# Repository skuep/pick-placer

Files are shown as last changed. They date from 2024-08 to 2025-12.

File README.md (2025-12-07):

Pick-Placer
===========
This is work in progress and highly beta.

Onshape CAD Data is here: https://cad.onshape.com/documents/7a2b90e013ddb4f790097381/w/de934a112d86b578c597cdf9/e/dd9aa8bcdc6310fd48dbadf3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

This is a mix of multiple projects:
---------

- LumenPnP
  - Basic Idea and Toolhead Design
  - Valves, 260mm Belt, Nema 11 Rotation Motors (later switched to Juki style from Robotdigg)
  - Cameras (ELP 720P USB kamera modul CMOS OV9712 mit 6mm Fokus) & ring-lights (slightly modified)
  - Staging plate (modified to measure 90x470)
  - Photon feeder support (mechanical, not tested)
  - Datum board & mount (modified)
  - Toolhead Linear Rails
  
- Voron Trident 350mm
  - Frame Kit (plus a few uncritical saw cuts and blind joint holes using jigs) and Panels
  - X/Y Motors, Belts, MGN12 and MGN9 Rails for X/Y
  - Nema14 stepper motor (~~17HS08-1004S~~ 17HS19-2004S1)
  - Split toolhead carriage design and XY joint design
  - X/Y Drag Chains
  - Idlers (BFI)
  - D2F homing switch PCB
  - Rubber feet
  - DIN Rails
  - Screws & Misc Hardware
  - Belt routing idea (plus some inspiration from VzBoT-330)

Other Parts used:
- Festo CRVZS-0,4 (Used on ebay)
- MGN9C 100mm Rails (CNA on AliExpress)
- Nema17 stepper motor with 20mm thickness (Stepper-Online) for Toolhead
- 500mm length extrusions with V groove for LumenPnP feeder compatibility
- 32 Teeth pulleys

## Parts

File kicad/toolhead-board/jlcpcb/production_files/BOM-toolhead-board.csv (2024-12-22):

Comment | Designator | Footprint | LCSC
100R | FB1 | R_0805_2012Metric | C1015
22u/10V/X5R | C10 | C_1206_3216Metric | C12891
10u/50V/X5R | C9 | C_1206_3216Metric | C13585
100n | C1,C11,C2,C8 | C_0603_1608Metric | C14663
UA9637 | U6 | SO-8_3.9x4.9mm_P1.27mm | C1544610
1n | C4,C5 | C_0603_1608Metric | C1588
4.7u/16V | C3 | C_0603_1608Metric | C19666
TLV6001DCK | U7,U8 | SOT-353_SC-70-5 | C2059411
MIC5233-5.0YM5-TR | U3 | SOT-23-5 | C219988
10R | R1,R11,R12,R15,R16,R2,R3,R6,R7,R8 | R_0603_1608Metric | C22859
5.1K | R10,R4,R5,R9 | R_0603_1608Metric | C23186
24K | R14 | R_0603_1608Metric | C23352
100K | R13 | R_0603_1608Metric | C25803
1uF/50V | C6 | C_0805_2012Metric | C28323
LMZM23601 | U5 | Texas_SIL0010A_MicroSiP-10-1EP_3.8x3mm_P0.6mm_EP0.7x2.9mm_ThermalVias | C2861484
74LVC1G17GW | U4 | SOT-353_SC-70-5 | C426705
USB_C_Receptacle_USB2.0 | J9 | MC-711 | C6332301
MountingHole | H3 | MountingHole_3.2mm_M3
MountingHole | H2 | MountingHole_3.2mm_M3
CAM | J10 | JST_PH_B4B-PH-K_1x04_P2.00mm_Vertical
RGB | J5 | JST_XH_B3B-XH-A_1x03_P2.50mm_Vertical
XGZP6857A100KPGPN | U2 | XGZP6857A
ZES | J8 | JST_PH_B4B-PH-K_1x04_P2.00mm_Vertical
MountingHole | H5 | MountingHole_3.2mm_M3
VR | J7 | JST_XH_B2B-XH-A_1x02_P2.50mm_Vertical
Conn_01x08 | J12 | JST_XH_S8B-XH-A-1_1x08_P2.50mm_Horizontal
DB9_Male_MountingHoles | J11 | DSUB-9_Male_Horizontal_P2.77x2.84mm_EdgePinOffset4.94mm_Housed_MountingHolesOffset7.48mm
VL | J6 | JST_XH_B2B-XH-A_1x02_P2.50mm_Vertical
XGZP6857A100KPGPN | U1 | XGZP6857A
MountingHole | H6 | MountingHole_3.2mm_M3
Conn_02x12_Top_Bottom | J1 | Molex_Micro-Fit_3.0_43045-2400_2x12_P3.00mm_Horizontal
RM | J4 | JST_XH_B4B-XH-A_1x04_P2.50mm_Vertical
ZM | J2 | JST_XH_B4B-XH-A_1x04_P2.50mm_Vertical
LM | J3 | JST_XH_B4B-XH-A_1x04_P2.50mm_Vertical

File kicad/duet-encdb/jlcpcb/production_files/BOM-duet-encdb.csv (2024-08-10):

Comment | Designator | Footprint | LCSC
1u/10V | C2,C5,C7 | C_0603_1608Metric | C15849
10u/10V | C1,C3,C4,C6 | C_0805_2012Metric | C15850
100R | R1,R2,R3,R4,R5,R6 | R_0603_1608Metric | C22775
10K | R10,R11,R12,R7,R8,R9 | R_0603_1608Metric | C25804
LM2775DSG | U1,U2 | WSON-8-1EP_2x2mm_P0.5mm_EP0.9x1.6mm_ThermalVias | C473361
74LVC541A | U3 | TSSOP-20_4.4x6.5mm_P0.65mm | C6093
Conn_01x08 | J3 | JST_XH_B8B-XH-A_1x08_P2.50mm_Vertical
Conn_01x08 | J2 | JST_XH_B8B-XH-A_1x08_P2.50mm_Vertical
Conn_02x05_Odd_Even | J1 | PinSocket_2x05_P2.54mm_Vertical

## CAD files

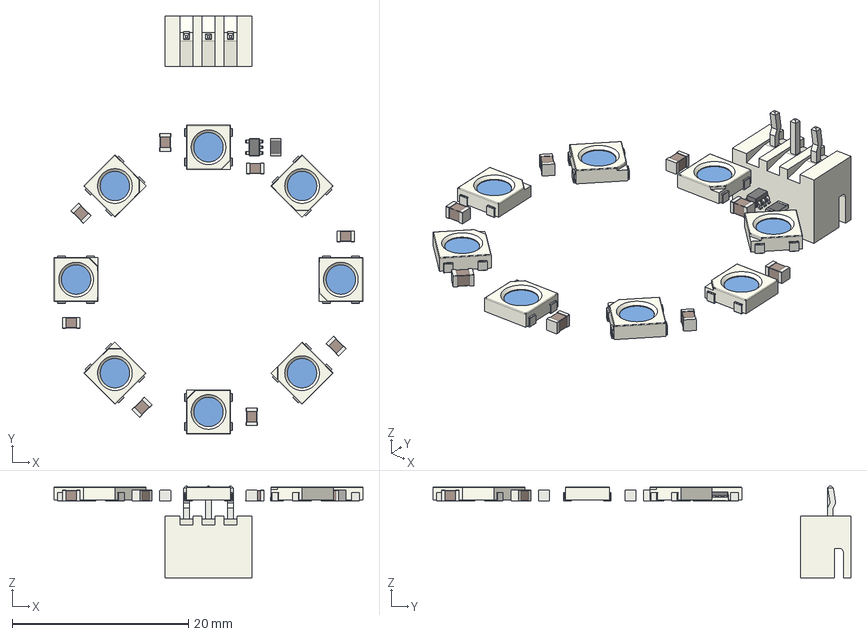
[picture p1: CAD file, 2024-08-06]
kicad/ring-light/ringLight.step
35.0 x 47.4 x 10.4 mm
ringLight PCB

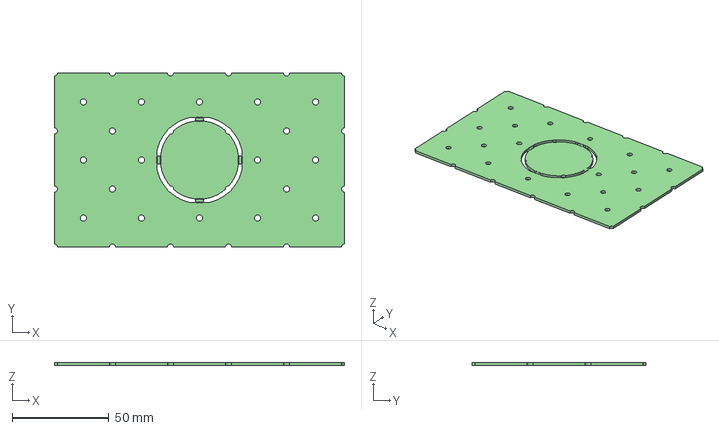
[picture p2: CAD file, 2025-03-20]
kicad/staging-plate/staging-plate-small-cam.step
149.8 x 89.8 x 1.59 mm

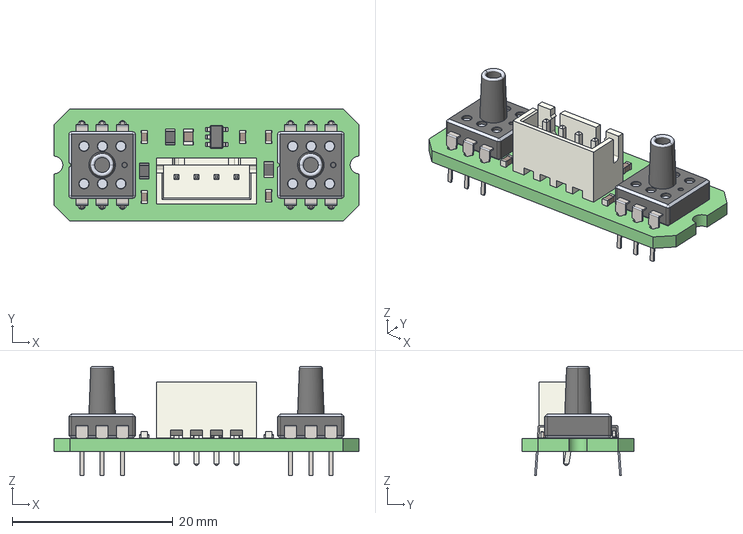
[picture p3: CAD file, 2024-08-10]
kicad/vacuum-sensor/vacuum-sensor.step
38.0 x 14.0 x 13.6 mm
_autosave-vacuum-sensor PCB

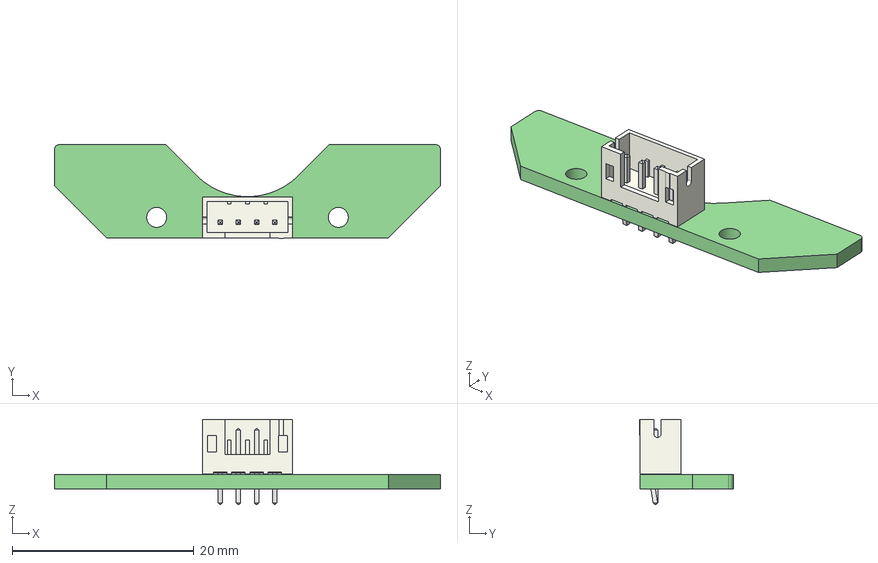
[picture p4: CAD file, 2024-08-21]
kicad/z-endstop/z-endstop.step
42.5 x 10.3 x 9.40 mm
z-endstop PCB

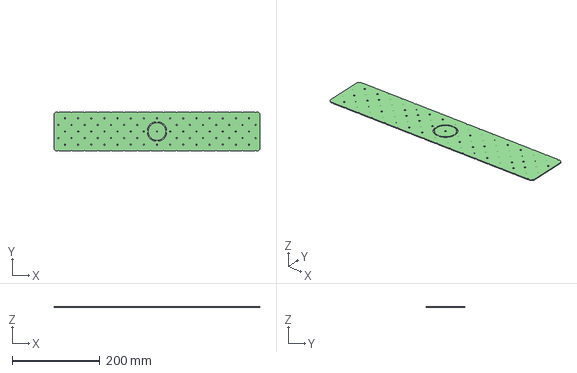
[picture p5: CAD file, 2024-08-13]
kicad/staging-plate/staging-plate.step
470.0 x 89.6 x 1.59 mm

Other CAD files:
kicad/staging-plate/staging-plate-small.step

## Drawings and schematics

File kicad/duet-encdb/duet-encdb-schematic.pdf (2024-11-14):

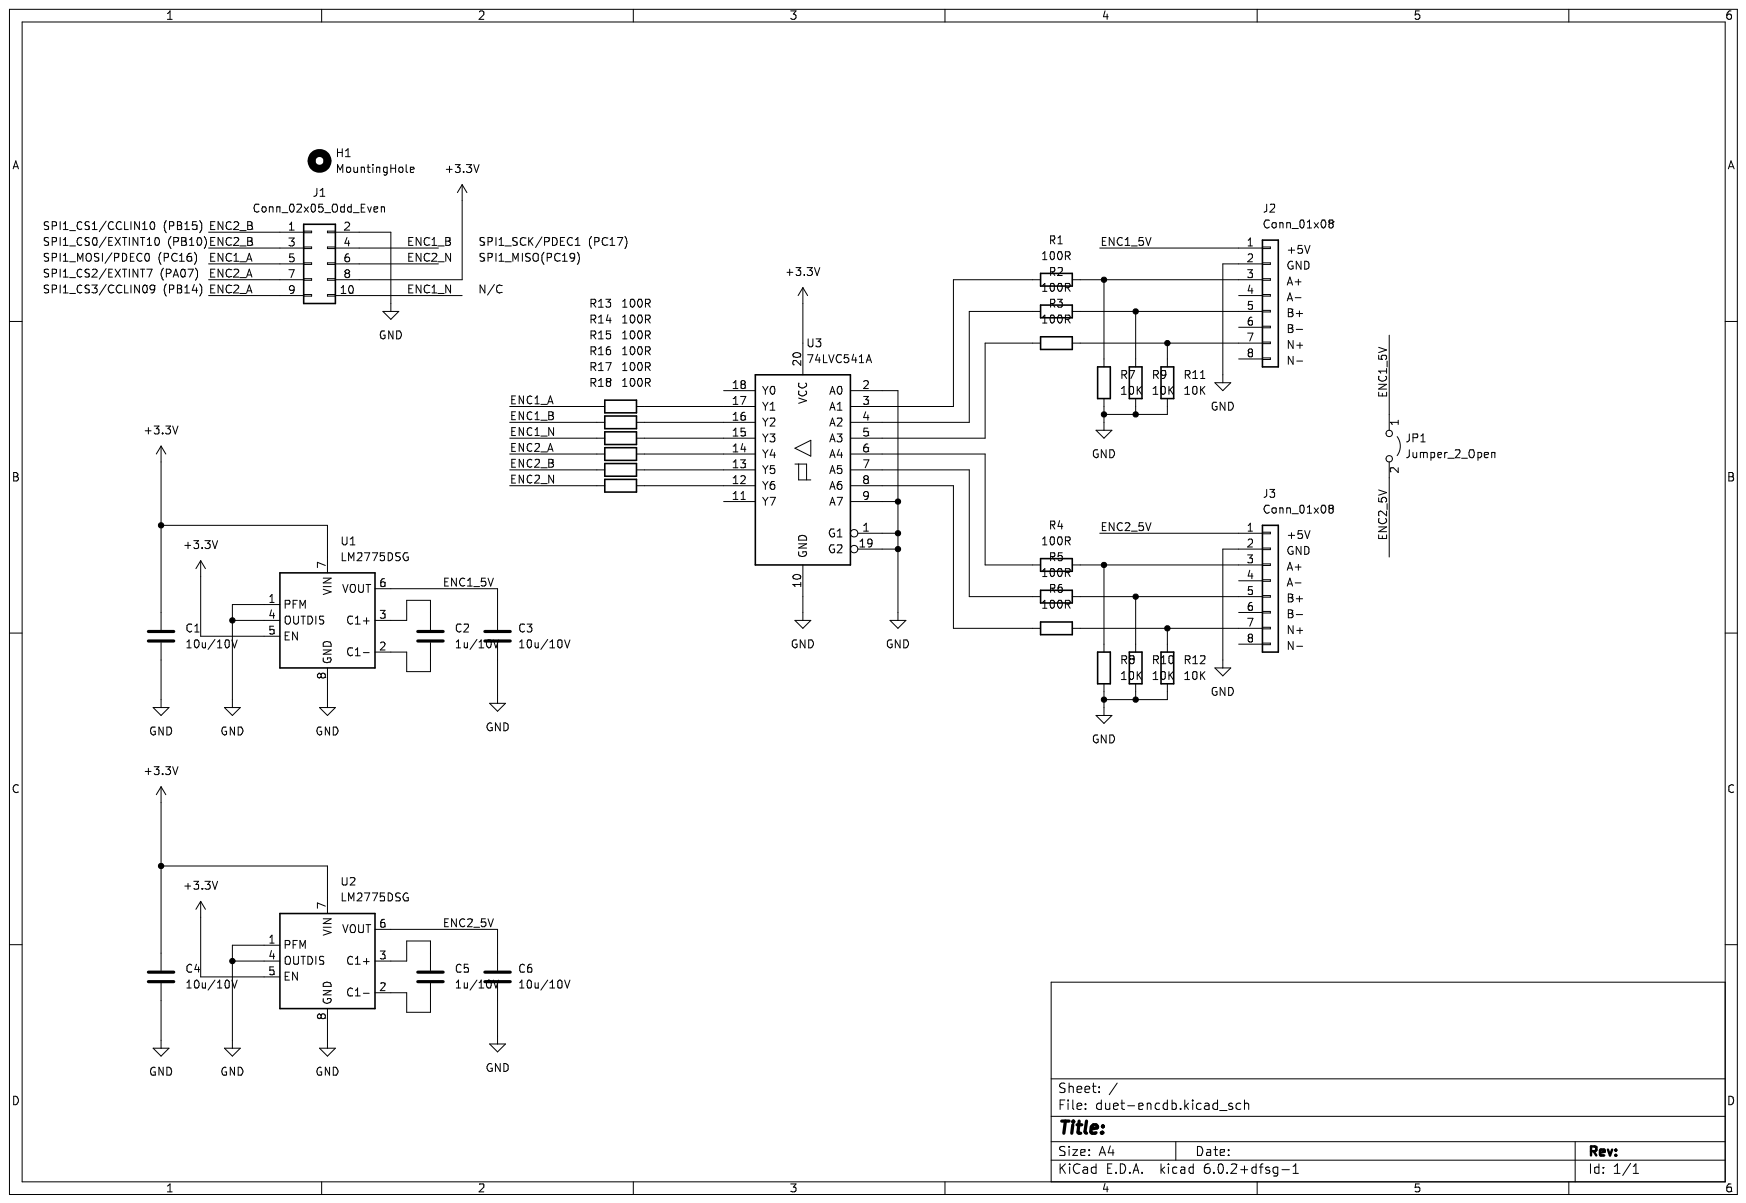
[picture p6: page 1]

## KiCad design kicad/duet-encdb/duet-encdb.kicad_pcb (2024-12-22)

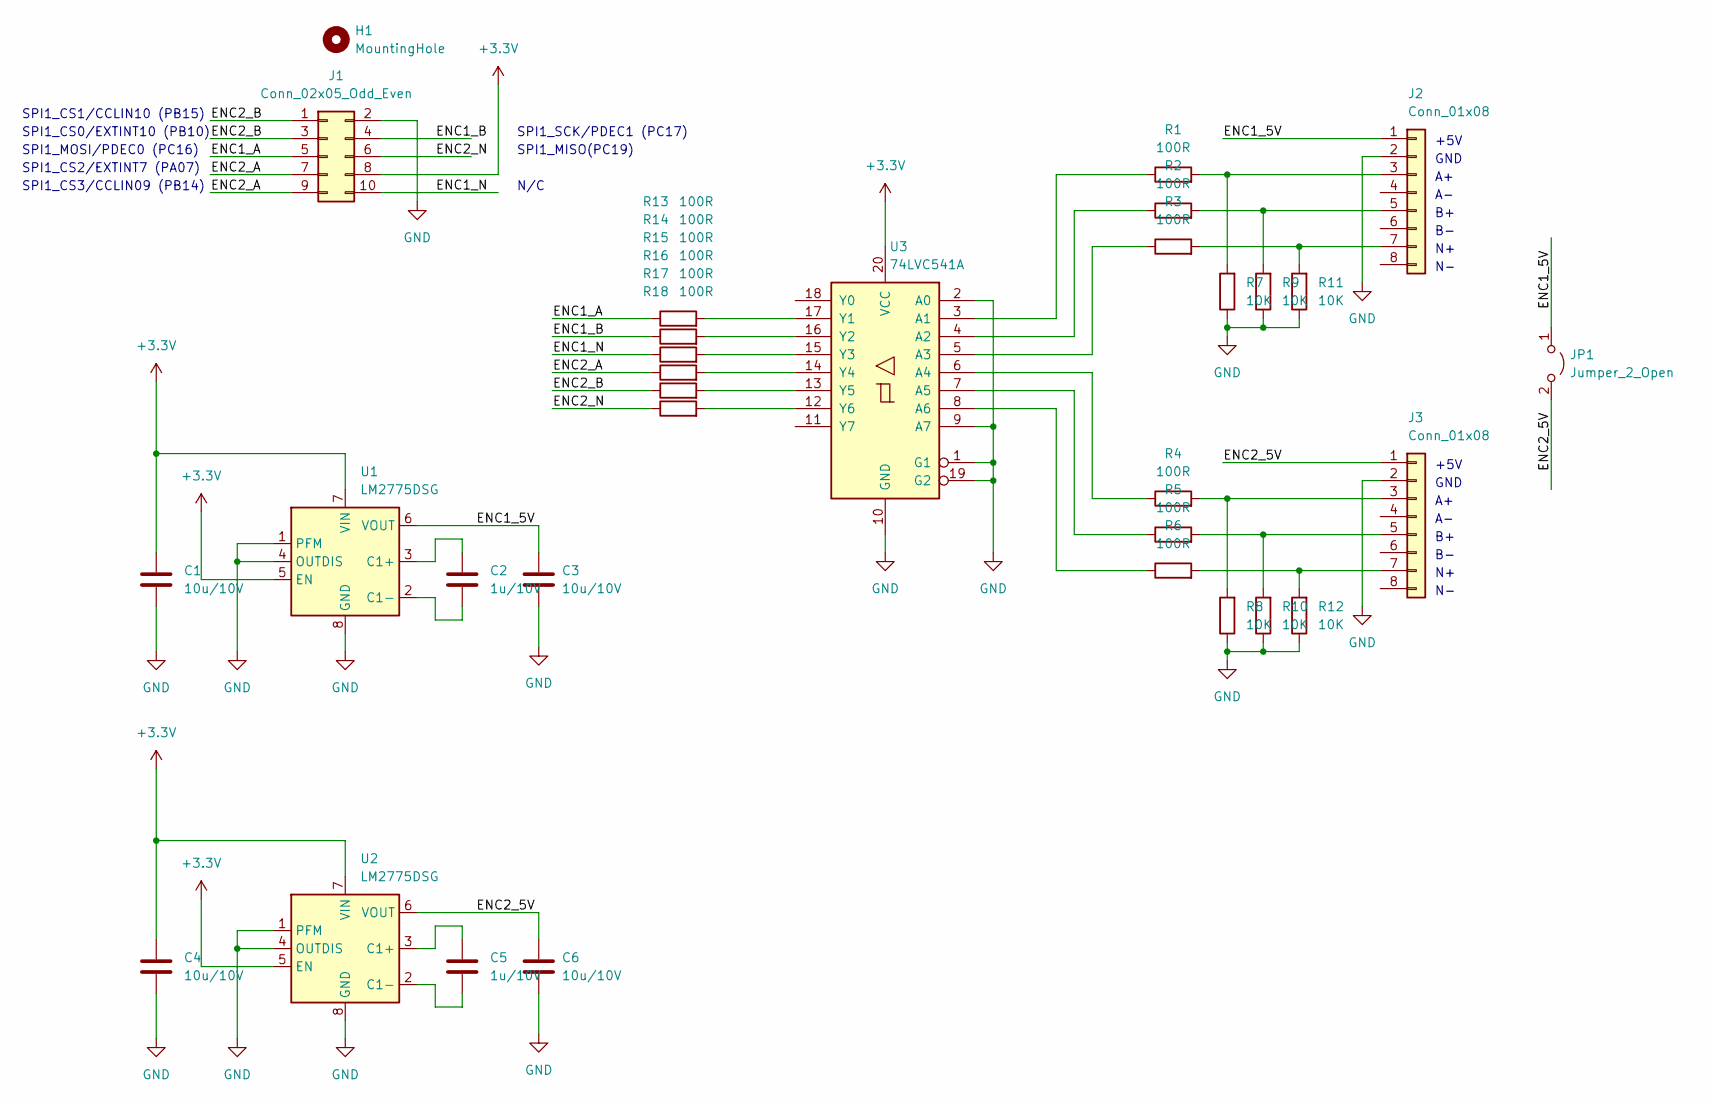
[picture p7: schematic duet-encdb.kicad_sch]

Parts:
C1, C3, C4, C6: 10u/10V; C_0805_2012Metric; LCSC C15850
C2, C5: 1u/10V; C_0603_1608Metric; LCSC C15849
H1: MountingHole; MountingHole_2.5mm
J1: Conn_02x05_Odd_Even; PinSocket_2x05_P2.54mm_Vertical
J2, J3: Conn_01x08; JST_XH_B8B-XH-A_1x08_P2.50mm_Vertical
JP1: Jumper_2_Open; SolderJumper-2_P1.3mm_Open_TrianglePad1.0x1.5mm
R1, R2, R3, R4, R5, R6, R13, R14, R15, R16, R17, R18: 100R; R_0603_1608Metric; LCSC C22775
R7, R8, R9, R10, R11, R12: 10K; R_0603_1608Metric; LCSC C25804
U1, U2: LM2775DSG; WSON-8-1EP_2x2mm_P0.5mm_EP0.9x1.6mm_ThermalVias; LCSC C473361
U3: 74LVC541A; TSSOP-20_4.4x6.5mm_P0.65mm; LCSC C6093

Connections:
+3V3: C1.1, C4.1, J1.8, U1.5 (EN), U1.7 (VIN), U2.5 (EN), U2.7 (VIN), U3.20 (VCC)
/ENC1_5V: C3.1, J2.1, JP1.1 (A), U1.6 (VOUT)
/ENC1_A: J1.5, R13.1
/ENC1_B: J1.4, R14.1
/ENC1_N: J1.10, R15.1
/ENC2_5V: C6.1, J3.1, JP1.2 (B), U2.6 (VOUT)
/ENC2_A: J1.7, J1.9, R16.1
/ENC2_B: J1.1, J1.3, R17.1
/ENC2_N: J1.6, R18.1
GND: C1.2, C3.2, C4.2, C6.2, J1.2, J2.2, J3.2, R7.1, R8.1, R9.1, R10.1, R11.1, R12.1, U1.1 (PFM), U1.4 (OUTDIS), U1.8 (GND), U1.9 (GND), U2.1 (PFM), U2.4 (OUTDIS), U2.8 (GND), U2.9 (GND), U3.1 (G1), U3.2 (A0), U3.9 (A7), U3.10 (GND), U3.19 (G2)
unnamed: C2.1, U1.3 (C1+)
unnamed: C2.2, U1.2 (C1-)
unnamed: C5.1, U2.3 (C1+)
unnamed: C5.2, U2.2 (C1-)
unnamed: J2.3, R1.2, R7.2
unnamed: J2.5, R2.2, R9.2
unnamed: J2.7, R3.2, R11.2
unnamed: J3.3, R4.2, R8.2
unnamed: J3.5, R5.2, R10.2
unnamed: J3.7, R6.2, R12.2
unnamed: R1.1, U3.3 (A1)
unnamed: R2.1, U3.4 (A2)
unnamed: R3.1, U3.5 (A3)
unnamed: R4.1, U3.6 (A4)
unnamed: R5.1, U3.7 (A5)
unnamed: R6.1, U3.8 (A6)
unnamed: R13.2, U3.17 (Y1)
unnamed: R14.2, U3.16 (Y2)
unnamed: R15.2, U3.15 (Y3)
unnamed: R16.2, U3.14 (Y4)
unnamed: R17.2, U3.13 (Y5)
unnamed: R18.2, U3.12 (Y6)

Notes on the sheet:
+5V
SPI1_MOSI/PDEC0 (PC16)
GND
SPI1_SCK/PDEC1 (PC17)
SPI1_MISO(PC19)
N/C
SPI1_CS2/EXTINT7 (PA07)
SPI1_CS3/CCLIN09 (PB14)
SPI1_CS0/EXTINT10 (PB10)
SPI1_CS1/CCLIN10 (PB15)

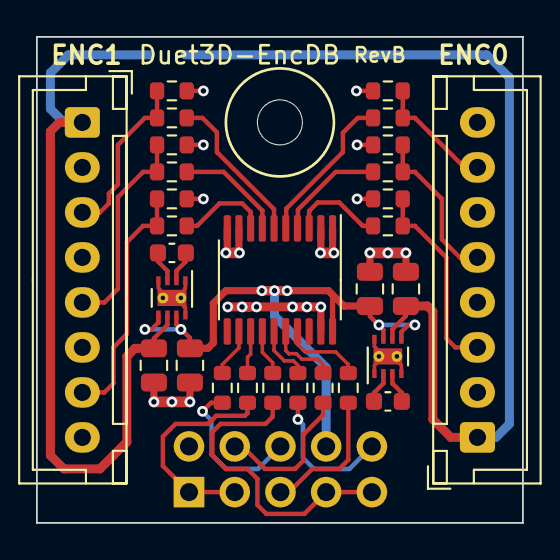
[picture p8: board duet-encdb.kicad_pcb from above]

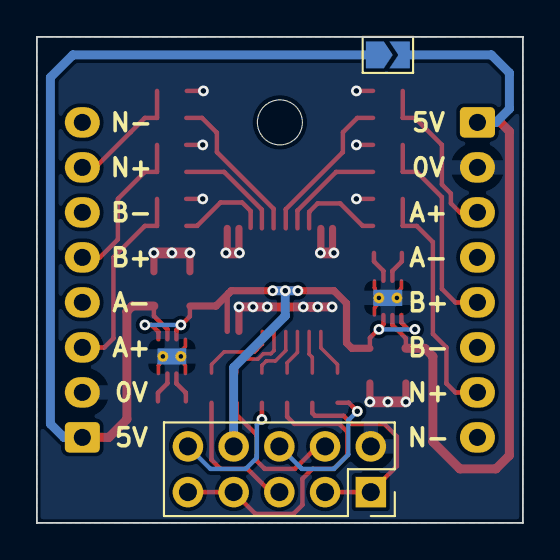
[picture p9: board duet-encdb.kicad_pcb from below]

Board: 2 copper layers, 27.0 x 27.0 mm, 32 parts (2 on the bottom side), 32 nets.

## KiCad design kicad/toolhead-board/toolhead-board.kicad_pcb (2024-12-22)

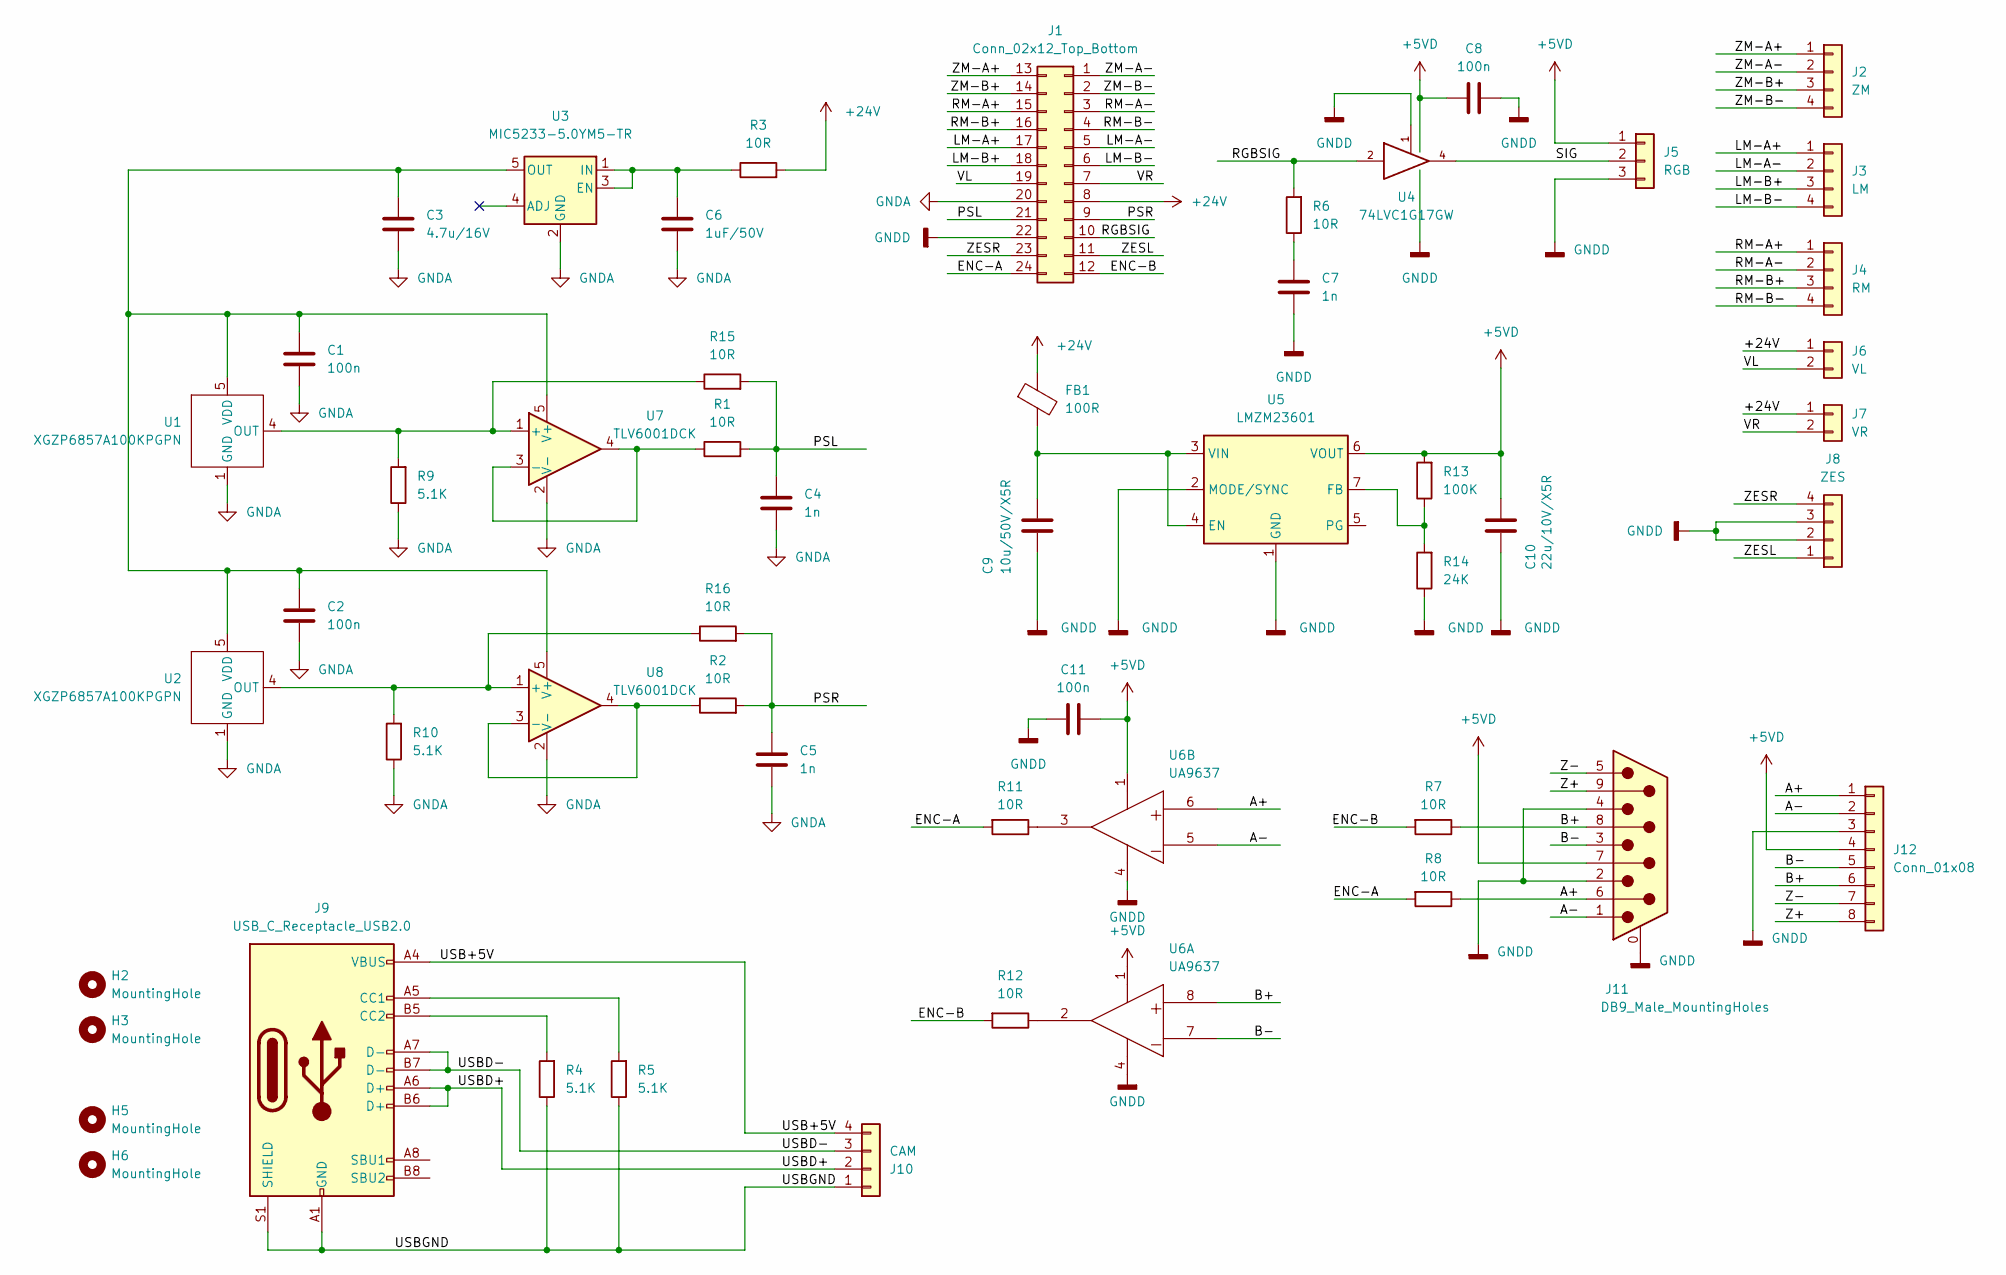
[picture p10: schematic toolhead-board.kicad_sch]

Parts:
C1, C2, C8, C11: 100n; C_0603_1608Metric; LCSC C14663
C3: 4.7u/16V; C_0603_1608Metric; LCSC C19666
C4, C5, C7: 1n; C_0603_1608Metric; LCSC C1588
C6: 1uF/50V; C_0805_2012Metric; LCSC C28323
C9: 10u/50V/X5R; C_1206_3216Metric; LCSC C13585
C10: 22u/10V/X5R; C_1206_3216Metric; LCSC C12891
FB1: 100R; R_0805_2012Metric; LCSC C1015
H2, H3, H5, H6: MountingHole; MountingHole_3.2mm_M3
J1: Conn_02x12_Top_Bottom; Molex_Micro-Fit_3.0_43045-2400_2x12_P3.00mm_Horizontal
J2: ZM; JST_XH_B4B-XH-A_1x04_P2.50mm_Vertical
J3: LM; JST_XH_B4B-XH-A_1x04_P2.50mm_Vertical
J4: RM; JST_XH_B4B-XH-A_1x04_P2.50mm_Vertical
J5: RGB; JST_XH_B3B-XH-A_1x03_P2.50mm_Vertical
J6: VL; JST_XH_B2B-XH-A_1x02_P2.50mm_Vertical
J7: VR; JST_XH_B2B-XH-A_1x02_P2.50mm_Vertical
J8: ZES; JST_PH_B4B-PH-K_1x04_P2.00mm_Vertical
J9: USB_C_Receptacle_USB2.0; MC-711; LCSC C6332301
J10: CAM; JST_PH_B4B-PH-K_1x04_P2.00mm_Vertical
J11: DB9_Male_MountingHoles; DSUB-9_Male_Horizontal_P2.77x2.84mm_EdgePinOffset4.94mm_Hou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
J12: Conn_01x08; JST_XH_S8B-XH-A-1_1x08_P2.50mm_Horizontal
R1, R2, R3, R6, R7, R8, R11, R12, R15, R16: 10R; R_0603_1608Metric; LCSC C22859
R4, R5, R9, R10: 5.1K; R_0603_1608Metric; LCSC C23186
R13: 100K; R_0603_1608Metric; LCSC C25803
R14: 24K; R_0603_1608Metric; LCSC C23352
U1, U2: XGZP6857A100KPGPN; XGZP6857A
U3: MIC5233-5.0YM5-TR; SOT-23-5; LCSC C219988
U4: 74LVC1G17GW; SOT-353_SC-70-5; LCSC C426705
U5: LMZM23601; Texas_SIL0010A_MicroSiP-10-1EP_3.8x3mm_P0.6mm_EP0.7x2.9mm_T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; LCSC C2861484
U6: UA9637; SO-8_3.9x4.9mm_P1.27mm; LCSC C1544610
U7, U8: TLV6001DCK; SOT-353_SC-70-5; LCSC C2059411

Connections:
+5VD: C8.1, C10.1, C11.2, J5.1, J11.7, J12.4, R13.2, U4.5 (VCC), U5.6 (VOUT), U6.1 (VCC)
+24V: FB1.1, J1.8, J6.1, J7.1, R3.2
/A+: J11.6, J12.1, R8.1, U6.6 (IN+)
/A-: J11.1, J12.2, U6.5 (IN-)
/B+: J11.8, J12.6, R7.1, U6.8 (IN+)
/B-: J11.3, J12.5, U6.7 (IN-)
/ENC-A: J1.24, R8.2, R11.2
/ENC-B: J1.12, R7.2, R12.2
/LM-A+: J1.17, J3.1
/LM-A-: J1.5, J3.2
/LM-B+: J1.18, J3.3
/LM-B-: J1.6, J3.4
/PSL: C4.1, J1.21, R1.2, R15.2
/PSR: C5.1, J1.9, R2.2, R16.2
/RGBSIG: J1.10, R6.2, U4.2
/RM-A+: J1.15, J4.1
/RM-A-: J1.3, J4.2
/RM-B+: J1.16, J4.3
/RM-B-: J1.4, J4.4
/SIG: J5.2, U4.4
/USB+5V: J9.A4 (VBUS), J9.A9 (VBUS), J9.B4 (VBUS), J9.B9 (VBUS), J10.4
/USBD+: J9.A6 (D+), J9.B6 (D+), J10.2
/USBD-: J9.A7 (D-), J9.B7 (D-), J10.3
/USBGND: J9.A1 (GND), J9.A12 (GND), J9.B1 (GND), J9.B12 (GND), J9.S1 (SHIELD), J10.1, R4.1, R5.1
/VL: J1.19, J6.2
/VR: J1.7, J7.2
/Z+: J11.9, J12.8
/Z-: J11.5, J12.7
/ZESL: J1.11, J8.1
/ZESR: J1.23, J8.4
/ZM-A+: J1.13, J2.1
/ZM-A-: J1.1, J2.2
/ZM-B+: J1.14, J2.3
/ZM-B-: J1.2, J2.4
GND: C7.2, C8.2, C9.2, C10.2, C11.1, J1.22, J5.3, J8.2, J8.3, J11.0 (PAD), J11.2, J11.4, J12.3, R14.1, U4.1, U4.3 (GND), U5.1 (GND), U5.2 (MODE/SYNC), U5.11 (GND), U6.4 (GND)
GNDA: C1.2, C2.2, C3.2, C4.2, C5.2, C6.2, J1.20, R9.1, R10.1, U1.1 (GND), U2.1 (GND), U3.2 (GND), U7.2 (V-), U8.2 (V-)
unnamed: C1.1, C2.1, C3.1, U1.5 (VDD), U2.5 (VDD), U3.5 (OUT), U7.5 (V+), U8.5 (V+)
unnamed: C6.1, R3.1, U3.1 (IN), U3.3 (EN)
unnamed: C7.1, R6.1
unnamed: C9.1, FB1.2, U5.3 (VIN), U5.4 (EN)
unnamed: J9.A5 (CC1), R5.2
unnamed: J9.B5 (CC2), R4.2
unnamed: R1.1, U7.3 (-), U7.4
unnamed: R2.1, U8.3 (-), U8.4
unnamed: R10.2, R16.1, U2.4 (OUT), U8.1 (+)
unnamed: R11.1, U6.3 (OUT)
unnamed: R12.1, U6.2 (OUT)
unnamed: R13.1, R14.2, U5.7 (FB)
unnamed: R9.2, R15.1, U1.4 (OUT), U7.1 (+)

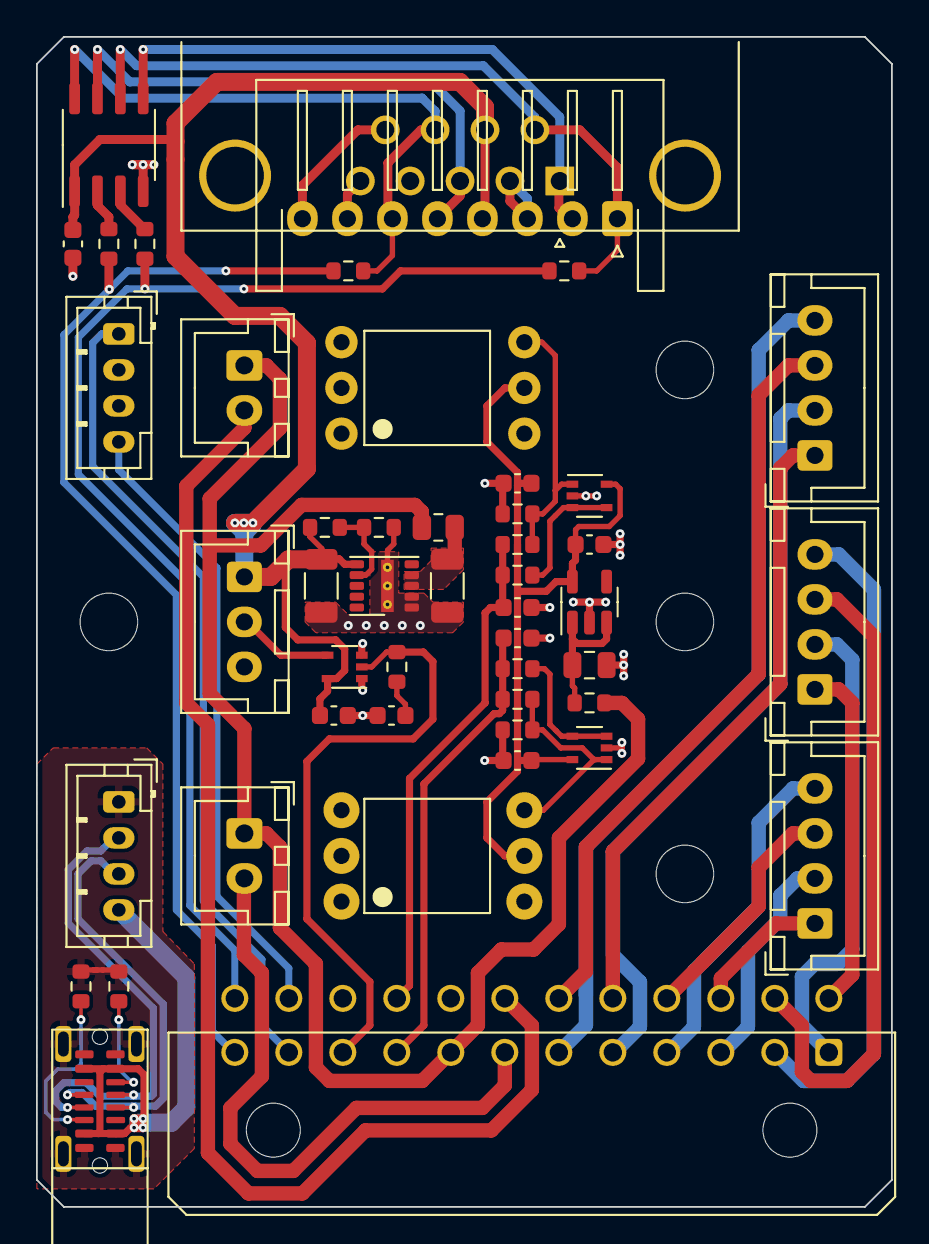
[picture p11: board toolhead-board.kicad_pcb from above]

Board: 2 copper layers, 47.5 x 65.0 mm, 52 parts (0 on the bottom side), 49 nets.

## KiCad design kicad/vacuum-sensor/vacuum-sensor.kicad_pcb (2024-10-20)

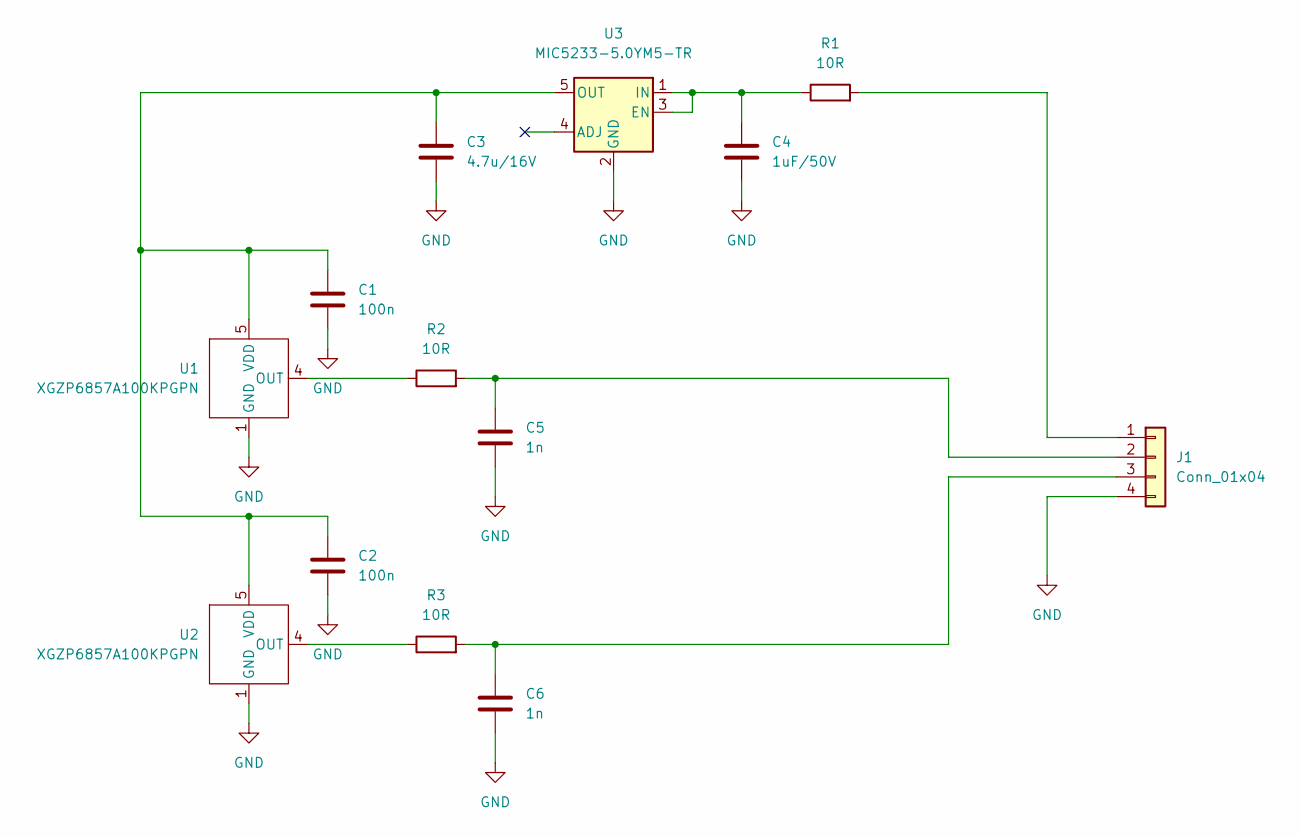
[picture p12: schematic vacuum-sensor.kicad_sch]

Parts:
C1, C2: 100n; C_0603_1608Metric; LCSC C14663
C3: 4.7u/16V; C_0603_1608Metric; LCSC C19666
C4: 1uF/50V; C_0805_2012Metric; LCSC C28323
C5, C6: 1n; C_0603_1608Metric; LCSC C1588
J1: Conn_01x04; JST_XH_B4B-XH-A_1x04_P2.50mm_Vertical
R1, R2, R3: 10R; R_0805_2012Metric; LCSC C17415
U1, U2: XGZP6857A100KPGPN; XGZP6857A
U3: MIC5233-5.0YM5-TR; SOT-23-5; LCSC C219988

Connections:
GND: C1.2, C2.2, C3.2, C4.2, C5.2, C6.2, J1.4, U1.1 (GND), U2.1 (GND), U3.2 (GND)
unnamed: C1.1, C2.1, C3.1, U1.5 (VDD), U2.5 (VDD), U3.5 (OUT)
unnamed: C4.1, R1.1, U3.1 (IN), U3.3 (EN)
unnamed: C5.1, J1.2, R2.2
unnamed: C6.1, J1.3, R3.2
unnamed: J1.1, R1.2
unnamed: R2.1, U1.4 (OUT)
unnamed: R3.1, U2.4 (OUT)

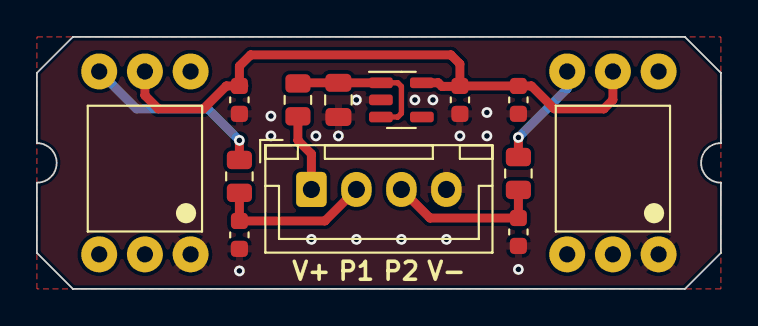
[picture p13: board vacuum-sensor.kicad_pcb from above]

Board: 2 copper layers, 38.0 x 14.0 mm, 13 parts (0 on the bottom side), 8 nets.

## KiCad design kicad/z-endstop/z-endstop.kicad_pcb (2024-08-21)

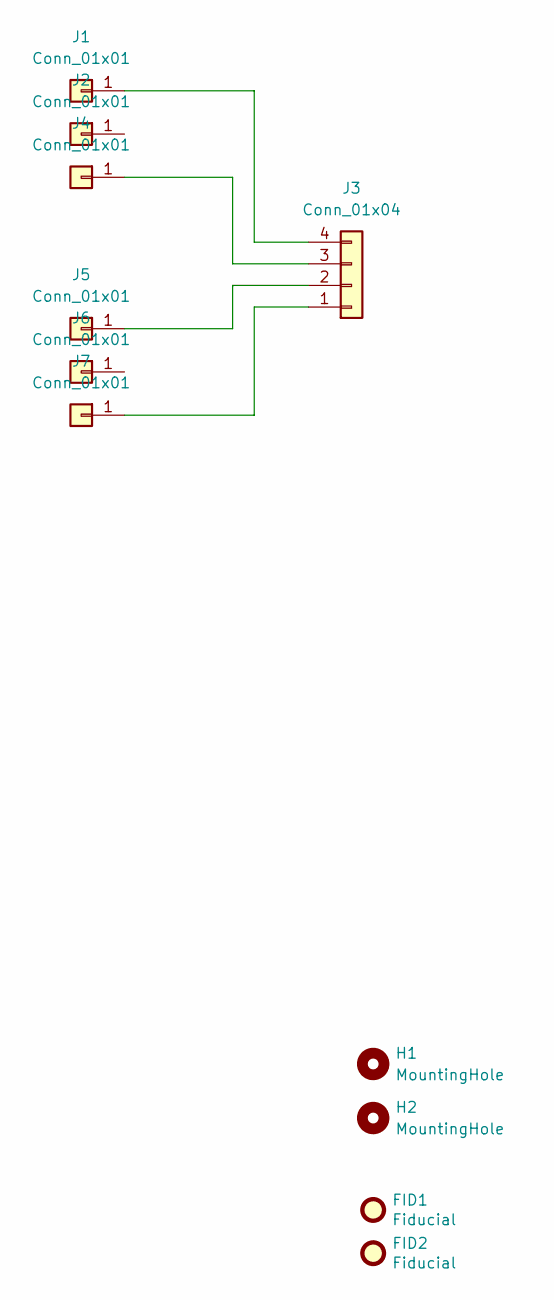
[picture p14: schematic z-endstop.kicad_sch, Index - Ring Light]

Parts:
FID1, FID2: Fiducial; Fiducial_1mm_Mask2mm
H1, H2: MountingHole; MountingHole_2.2mm_M2_DIN965_Pad_TopOnly
J1, J2, J4, J5, J6, J7: Conn_01x01; TestPoint_Pad_3.0x3.0mm
J3: Conn_01x04; JST_PH_B4B-PH-K_1x04_P2.00mm_Vertical

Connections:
unnamed: J1.1, J3.4
unnamed: J3.1, J7.1
unnamed: J3.2, J5.1
unnamed: J3.3, J4.1

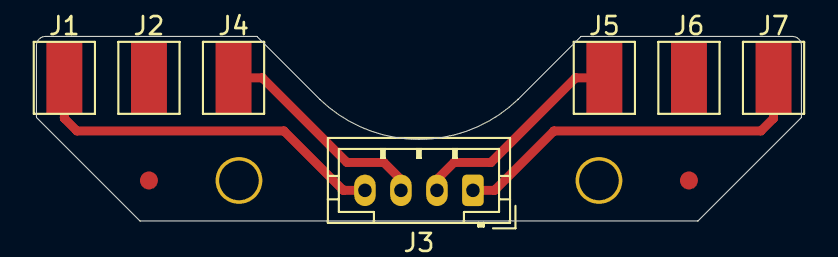
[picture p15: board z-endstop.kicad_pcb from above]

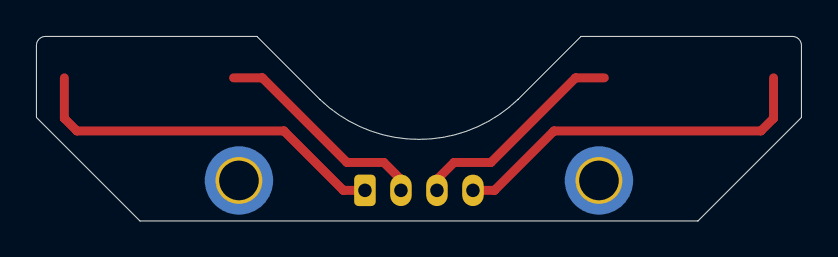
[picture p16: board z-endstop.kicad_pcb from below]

Board: 2 copper layers, 42.5 x 10.2 mm, 11 parts (2 on the bottom side), 4 nets.

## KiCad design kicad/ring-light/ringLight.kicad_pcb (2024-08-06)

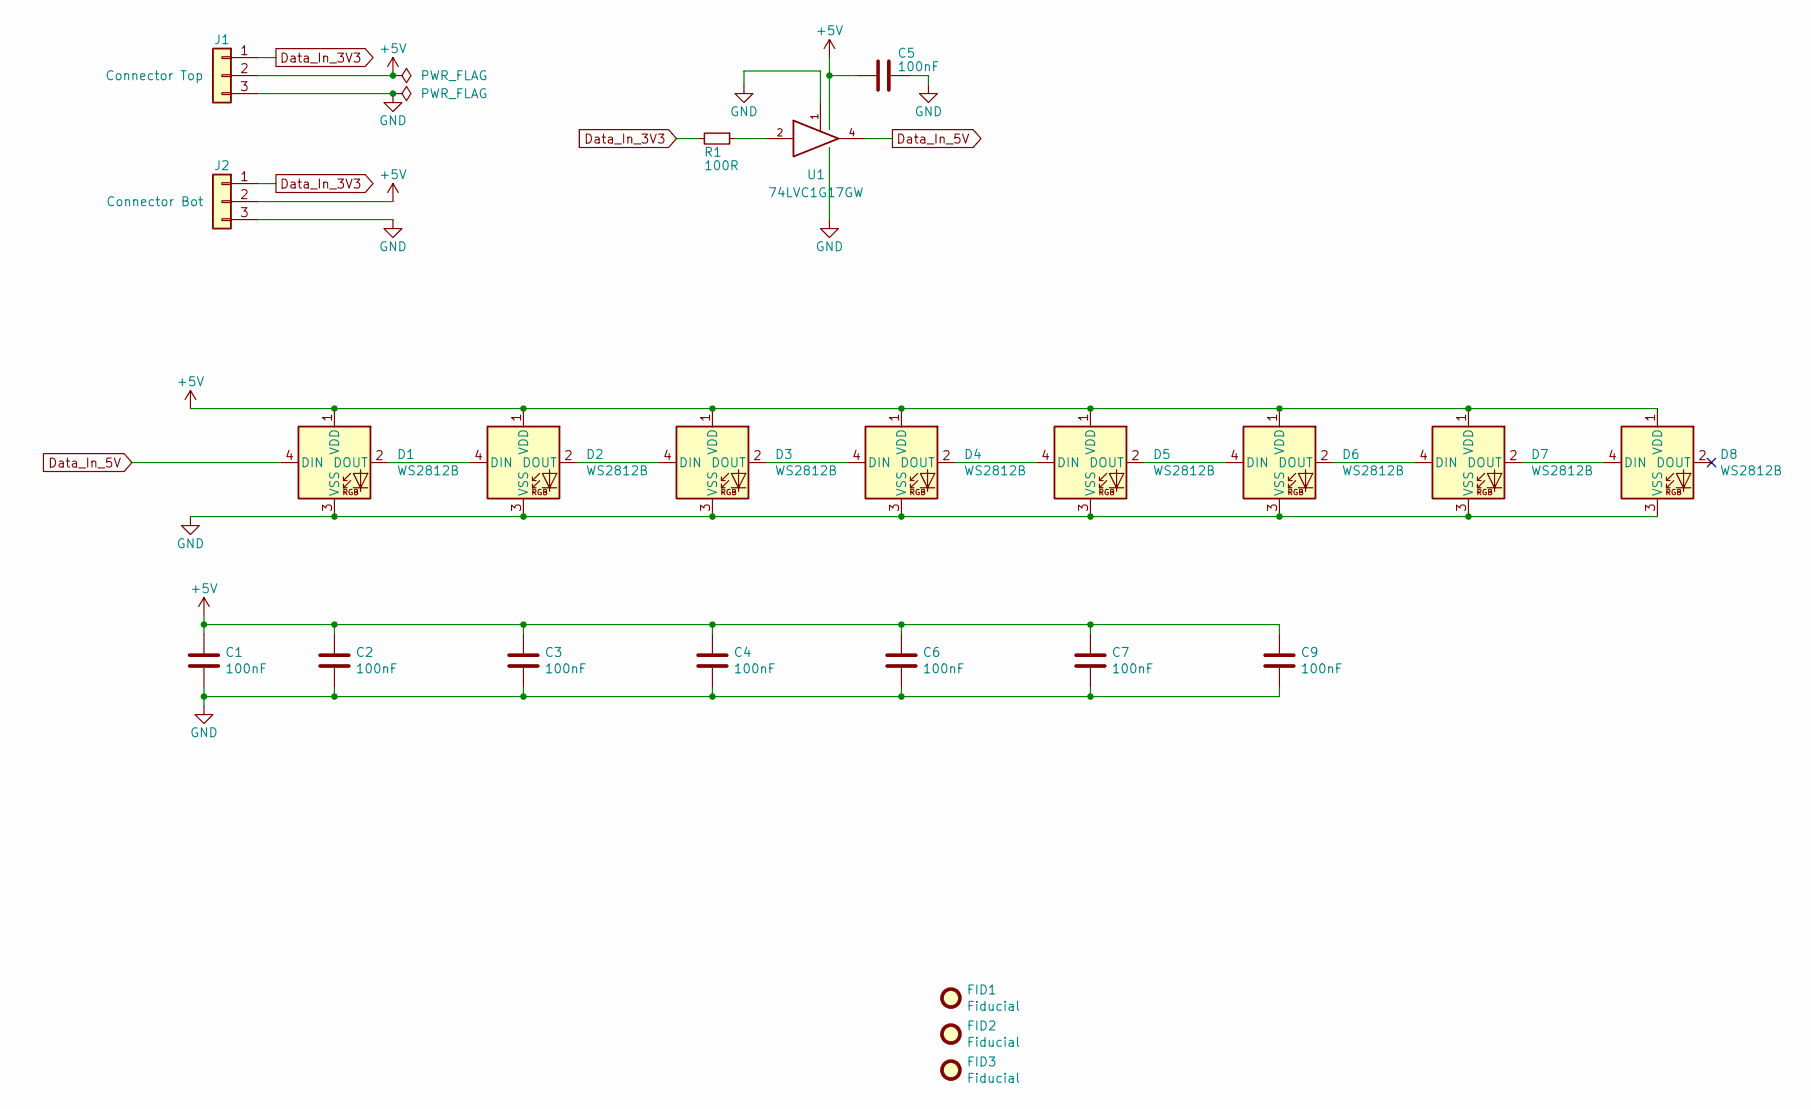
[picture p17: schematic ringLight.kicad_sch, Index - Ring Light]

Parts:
C1, C2, C3, C4, C5, C6, C7, C9: 100nF; C_0805_2012Metric; Part # CC0805KRX7R9BB104; JLCPCB C49678
D1, D2, D3, D4, D5, D6, D7, D8: WS2812B; LED_WS2812B_PLCC4_5.0x5.0mm_P3.2mm; Part # WS2812B; LCSC C2843785
FID1, FID2, FID3: Fiducial; Fiducial_1mm_Mask2mm
J1: Connector Top; JST_XH_B3B-XH-A_1x03_P2.50mm_Vertical; Part # B3B-XH-A(LF)(SN); JLCPCB C144394
J2: Connector Bot; JST_XH_S3B-XH-A-1_1x03_P2.50mm_Horizontal; Part # S3B-XH-A-1(LF)(SN); JLCPCB C163036
R1: 100R; R_0805_2012Metric; Part # 0805W8F1000T5E; LCSC C17408
U1: 74LVC1G17GW; SOT-353_SC-70-5; LCSC C426705

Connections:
+5V: C1.1, C2.1, C3.1, C4.1, C5.1, C6.1, C7.1, C9.1, D1.1 (VDD), D2.1 (VDD), D3.1 (VDD), D4.1 (VDD), D5.1 (VDD), D6.1 (VDD), D7.1 (VDD), D8.1 (VDD), J1.2, J2.2, U1.5 (VCC)
Data_In_3V3: J1.1, J2.1, R1.2
Data_In_5V: D1.4 (DIN), U1.4
GND: C1.2, C2.2, C3.2, C4.2, C5.2, C6.2, C7.2, C9.2, D1.3 (VSS), D2.3 (VSS), D3.3 (VSS), D4.3 (VSS), D5.3 (VSS), D6.3 (VSS), D7.3 (VSS), D8.3 (VSS), J1.3, J2.3, U1.1, U1.3 (GND)
unnamed: D1.2 (DOUT), D2.4 (DIN)
unnamed: D2.2 (DOUT), D3.4 (DIN)
unnamed: D3.2 (DOUT), D4.4 (DIN)
unnamed: D4.2 (DOUT), D5.4 (DIN)
unnamed: D5.2 (DOUT), D6.4 (DIN)
unnamed: D6.2 (DOUT), D7.4 (DIN)
unnamed: D7.2 (DOUT), D8.4 (DIN)
unnamed: R1.1, U1.2

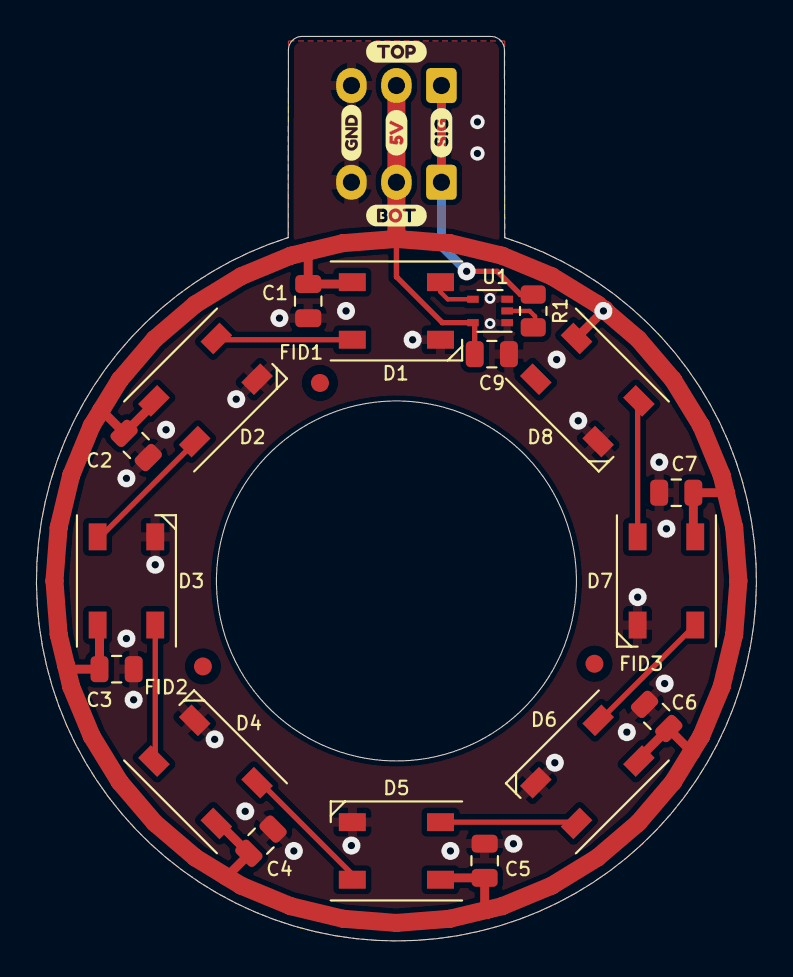
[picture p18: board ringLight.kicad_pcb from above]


Board: 2 copper layers, 40.0 x 50.2 mm, 35 parts (8 on the bottom side), 12 nets.

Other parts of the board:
LOGO: LOGO; logo
kibuzzard-61F2BC8D, kibuzzard-61F2BC8D#2: G***; kibuzzard-61F2BC8D
kibuzzard-61F2BC9E, kibuzzard-61F2BC9E#2: G***; kibuzzard-61F2BC9E
kibuzzard-61F2BC96, kibuzzard-61F2BC96#2: G***; kibuzzard-61F2BC96
kibuzzard-61F2BEFE: G***; kibuzzard-61F2BEFE
kibuzzard-61F2BF3C: G***; kibuzzard-61F2BF3C
kibuzzard-61F2BF4A: G***; kibuzzard-61F2BF4A
kibuzzard-61F2BF10: G***; kibuzzard-61F2BF10
svg2mod: n/a; label

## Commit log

2024-07-31 Added ring-light PCB
    [ringLight.kicad_pcb, ringLight.kicad_sch, ringLight.step]
2024-07-31 Modified staging plate dimensions
    [staging-plate.kicad_pcb, staging-plate.kicad_sch, staging-plate.step]
2024-07-31 Added datum board
    [datum.kicad_pcb, datum.kicad_sch]
2024-08-04 Generation of production data
    [datum.kicad_pcb, datum.kicad_sch]
2024-08-06 Changed buffer to schmitt trigger type
    [ringLight.kicad_pcb, ringLight.kicad_sch, ringLight.step]
2024-08-10 Added daughterboard for dual encoder
    [BOM-duet-encdb.csv, duet-encdb.kicad_pcb, duet-encdb.kicad_sch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]
2024-08-10 Added vacuum sensor board for toolhead
    [BOM-vacuum-sensor.csv, vacuum-sensor.kicad_pcb, vacuum-sensor.kicad_sch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]
2024-08-10 Added step file to encoder daughterboard
    [duet-encdb.kicad_pcb]
2024-08-10 Added second optionalk connector
    [BOM-vacuum-sensor.csv, vacuum-sensor.kicad_pcb, vacuum-sensor.kicad_sch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]
2024-08-10 Minor changes
    [BOM-vacuum-sensor.csv, vacuum-sensor.kicad_pcb, vacuum-sensor.kicad_sch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]
2024-08-13 Changed to 1.6mm thickness as that is enough and easy to source
    [staging-plate.kicad_pcb, staging-plate.step]
2024-08-21 Added Z-endstop PCB
    [z-endstop.kicad_pcb, z-endstop.kicad_sch, z-endstop.step]
2024-10-20 Fixed orientation
    [vacuum-sensor.kicad_pcb]
2024-11-01 Initial commit toolhead board
    [toolhead-board.kicad_pcb, toolhead-board.kicad_sch]
2024-11-02 Added RS422 receiver
    [toolhead-board.kicad_pcb, toolhead-board.kicad_sch]
2024-11-02 Final touches and gerber data generation
    [BOM-toolhead-board.csv, toolhead-board.kicad_pcb, toolhead-board.kicad_sch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]
2024-11-03 Moved mounting holes
    [toolhead-board.kicad_pcb]
2024-11-03 Correct footprint for 0603 resistor
    [BOM-toolhead-board.csv, toolhead-board.kicad_pcb, toolhead-board.kicad_sch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]
2024-11-08 Added EncDB schematic
2024-11-09 Bumped to RevB, added series resistors to 10 pin header to not short out SPI pins during initialization
    [duet-encdb.kicad_pcb, duet-encdb.kicad_sch]
2024-11-14 Changed pinout of header, because for the CCL decoder to work, we need to place A and B signals on CCLIN and EXTINT pins simultaneously
    [duet-encdb.kicad_pcb, duet-encdb.kicad_sch]
2024-12-22 Removed C7 on RGB line
    [BOM-toolhead-board.csv, toolhead-board.kicad_pcb, toolhead-board.kicad_sch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]
2024-12-22 Changed naming of ENC0/1 to ENC1/2
    [duet-encdb.kicad_pcb]
2025-03-20 Added small staging plate
    [staging-plate-small.kicad_pcb, staging-plate-small.step]
2025-03-20 Added small plate with cam breakout
    [staging-plate-small-cam.kicad_pcb, staging-plate-small-cam.step]
2025-12-24 Switched to 0.5mm fiducial
    [datum.kicad_pcb]
